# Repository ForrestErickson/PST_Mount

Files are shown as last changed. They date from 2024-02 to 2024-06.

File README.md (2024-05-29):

# Mount for Personal Solar Telescope
**WARNING NEVER LOOK AT THE SUN THROUGH A TELESCOPE, BINOCULARS, NAKED EYE, unless you have a known safe solar filter and you know how to use it.** 
Never make a home made filter out of unknown materials.  
Galileo was blind at the end of his life. I do not know how he observed sun spots, but he did. And he went blind. 

## Motivation
Several friends in the Smoky Mountain Astronomical Society, aka **[SMAS](https://groups.io/g/smokymtnastro)**, have the Coronado PST.  
I am hoping to help make them easier to use.  
I watched them try to use a camera tripod where the user has to loosen both the altitude and the azimuth axis by turning knobs, and then move the telescope in both axis to recenter the sun and then tighten both axis hoping that there is not stored spring energy (flex) in the tripod legs and then letting go only to have the sun poorly centered. Visitors at public events where the telescope owners wanted to share the experience were more often away from the eye piece than looking through it as the telescope owner was frequently repointing the telescope.
A tripod with a mass mounted to it forms something similar to a torsion pendulum and once disturbed it can take some time for oscillations do die down and novice observers bumping the telescope set them right back into motion.

The limited required altitude range of a solar telescope (only about 23 degrees above and below the celestial equator allows a small and sturdy table-top equatorial mount form factor which I set about to develop.

## CAD Drawing
Here is a photo made of the prototype part way through the development.


I want to not only build one or more mounts but share my work widely and so have placed my files and work on Github.
I used the free and open source 3D CAD modeling software FreeCAD to draw the parts and to combine them into an assembly to make the mount.

Of the first things I did was to model the Coronado Personal Solar Telescope starting with a sketch I found on the internet and with dimensions taken from a real telescope by one of the club members.
Made from measurements off a real PST 
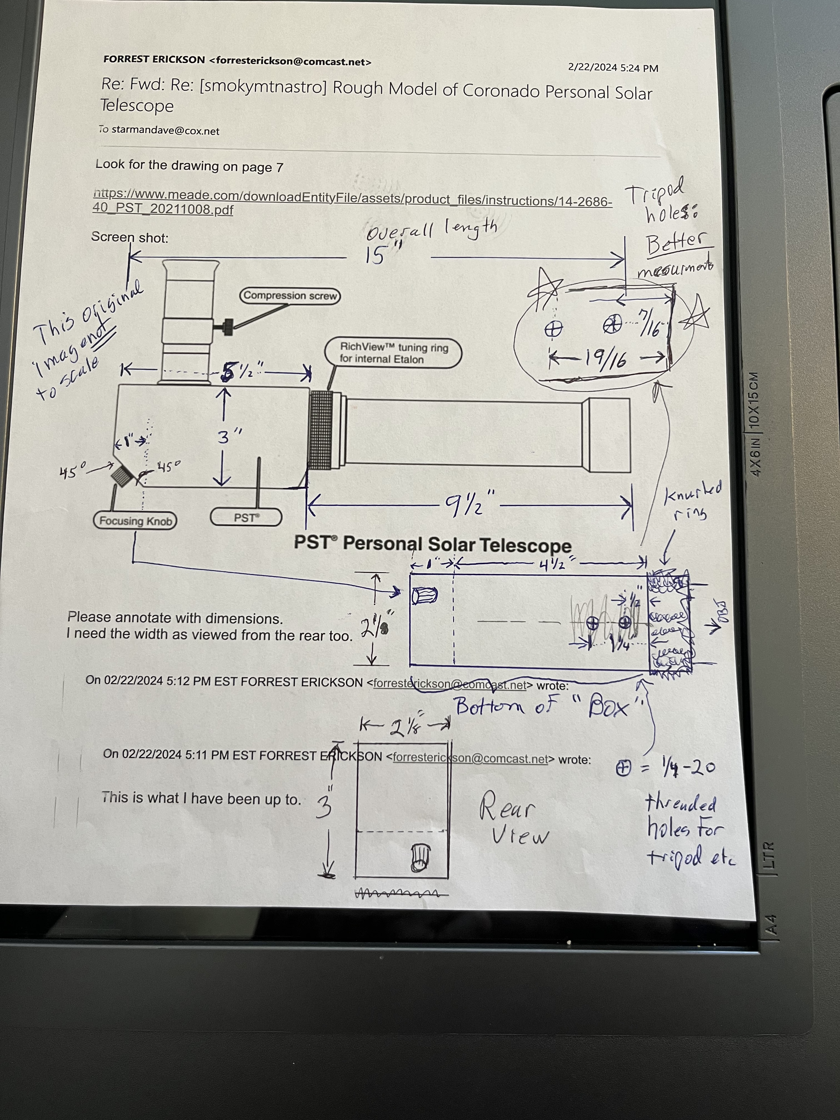
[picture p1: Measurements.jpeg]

From this drawing I made a 3D model of the body of the telescope (all but the long optical tube) and printed it out with an amusingly hollow body. TO this body I attached a cardboard tube approximating (but a bit smaller) than the real optical tube. 

## Prototype
An isometric view of  
<a
href="FabricationPhotos/WithWedgeIso.jpg">Image of: an isometric view.  
</a>

## Project Summary
* Drawn in FreeCAD and using A2Plus work bench.  
* Drawing for the PST (Personal Solar Telescope) is only from a side view photograph and will not be accurate.  A part was 3D printed to help with my trial and error fabrication and iterative design.  
* The size of the base is arbitrarily based on a 254 mm (10") disk (Hexagon) about 12.5 mm (1/2") thick.  Base set for latitude near Maryville TN of 35.5 Degrees.
* Right Assention Pin is 1/4" (About 25.4 /4 mm).
* Before the 20240408 solar eclipse I fabricated four of these and got three into the hands of PST users so that they might benifit during the eclipse.  

## License and Warranty
  **License**: This project and files are dedicated and released to the public domain.  
  **Warranty:** This project and files are designed to kill you and render the earth uninhabitable, however they not guaranteed to do so.

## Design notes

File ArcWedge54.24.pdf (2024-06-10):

Wedge 54.24 degrees.

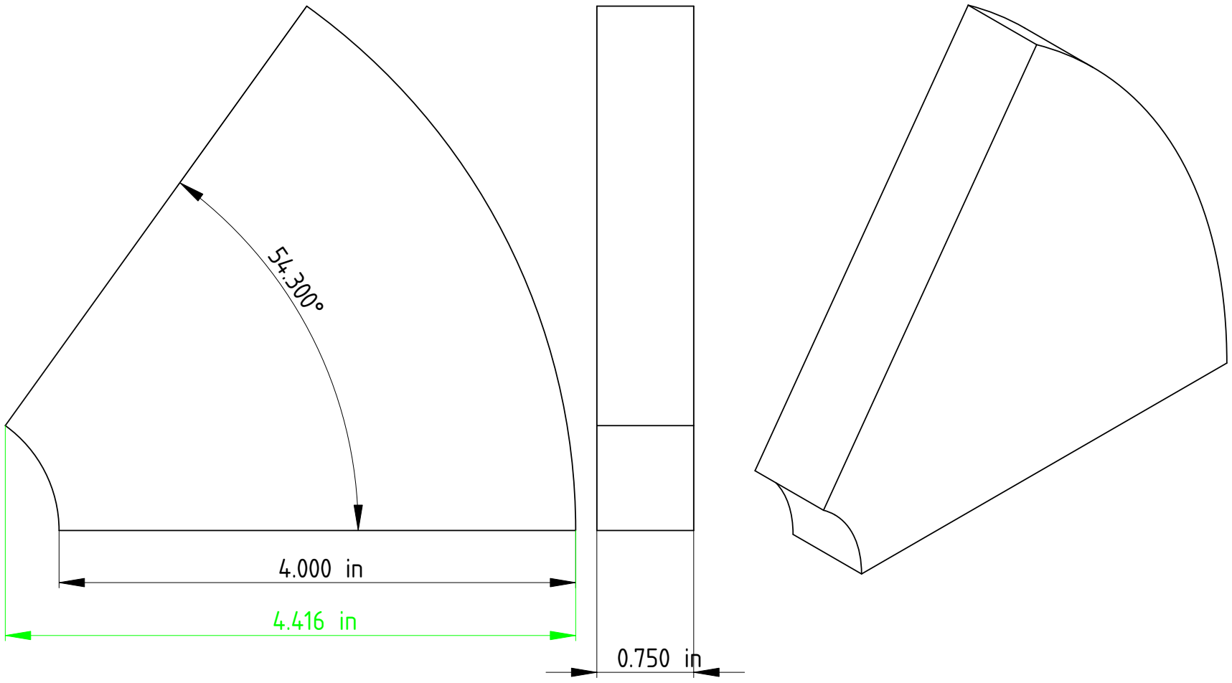
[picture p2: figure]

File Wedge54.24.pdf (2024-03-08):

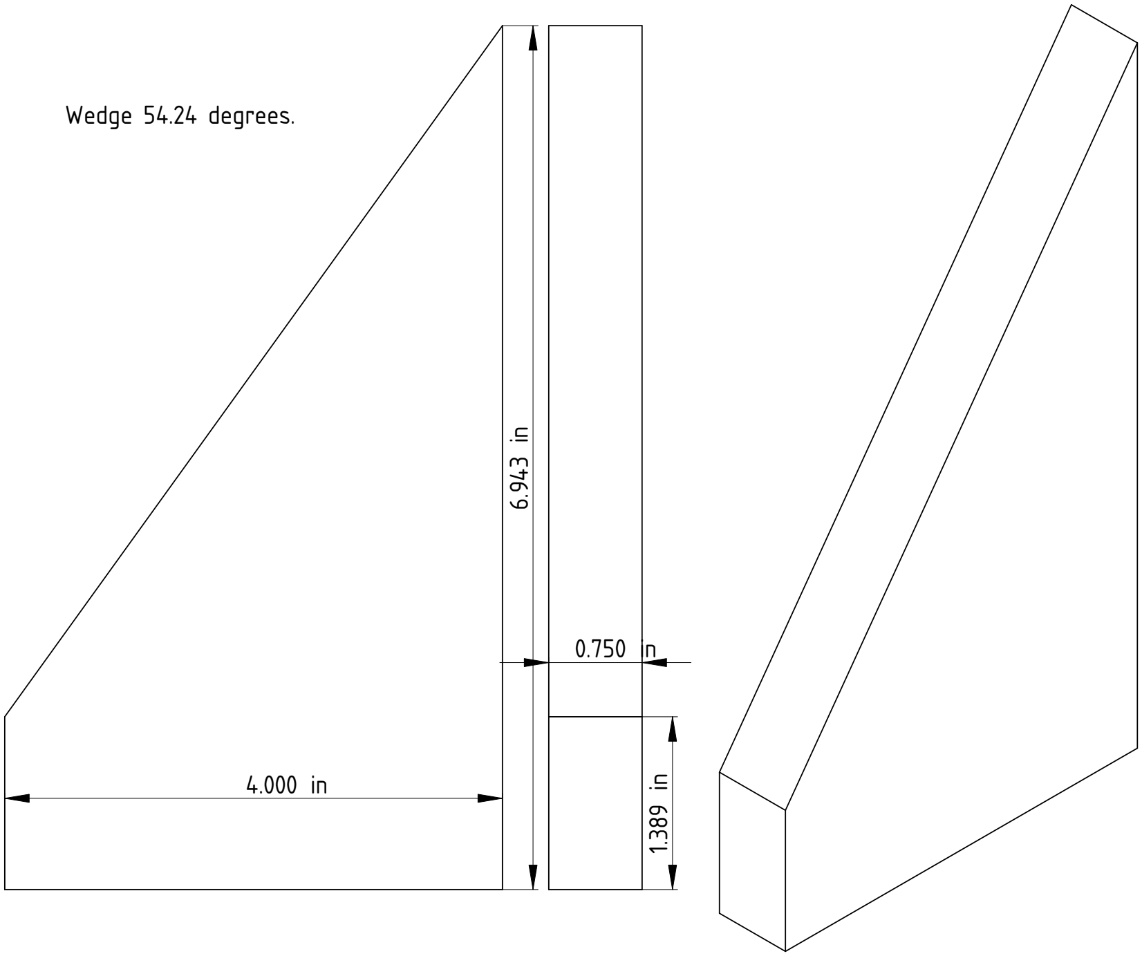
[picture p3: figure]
Wedge 54.24 degrees.

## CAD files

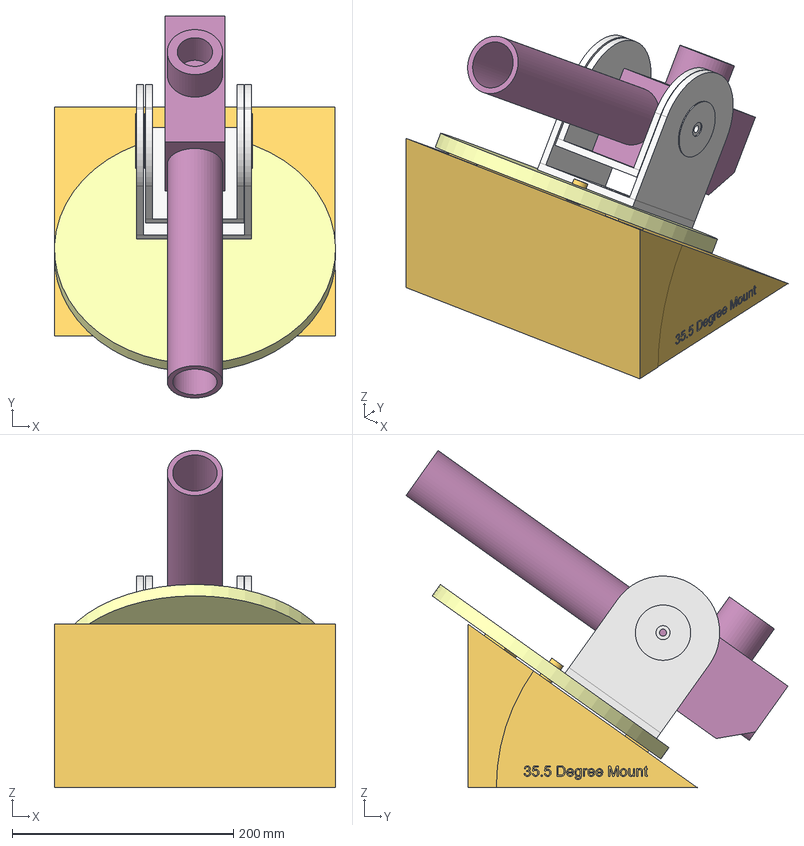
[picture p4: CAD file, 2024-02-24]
RAMountAssy_PST.FCStd
254.0 x 345.1 x 304.5 mm
Base35.5Degree_001
RAdisk_001
Pivot_Altitude_PST_001
Pivot_Fork_001
PST_Only_001

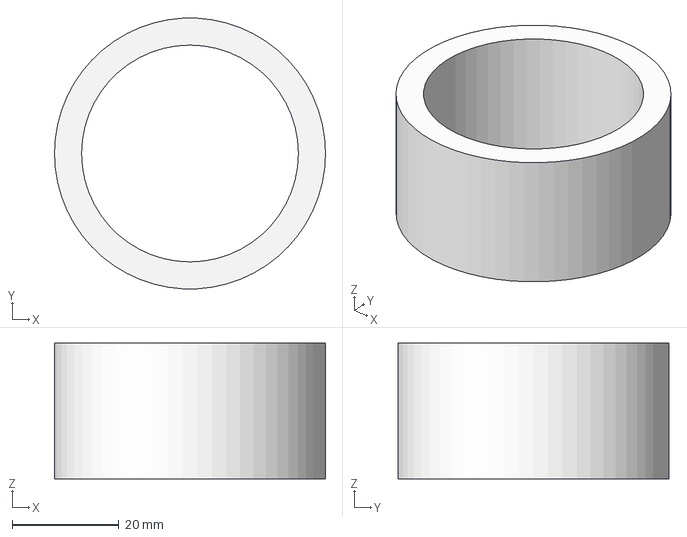
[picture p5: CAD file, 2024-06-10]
AdaptCardboardTube-Body.step
50.8 x 50.7 x 25.4 mm

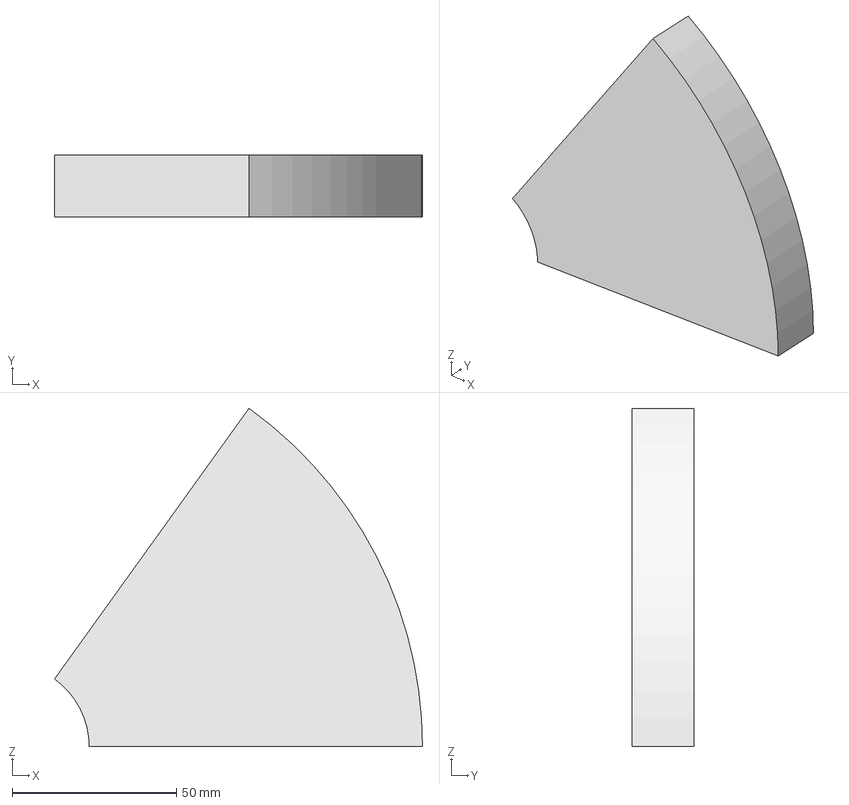
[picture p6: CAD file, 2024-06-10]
ArcWedge54.24Degrees.FCStd
112.2 x 19.1 x 103.1 mm

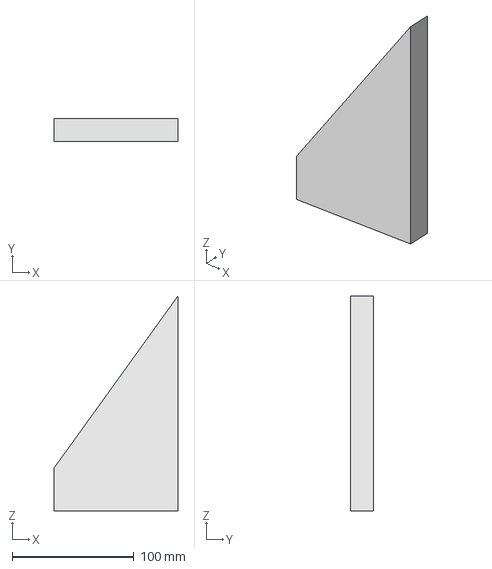
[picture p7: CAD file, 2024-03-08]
Wedge54.24Degrees.FCStd
101.6 x 19.1 x 176.3 mm

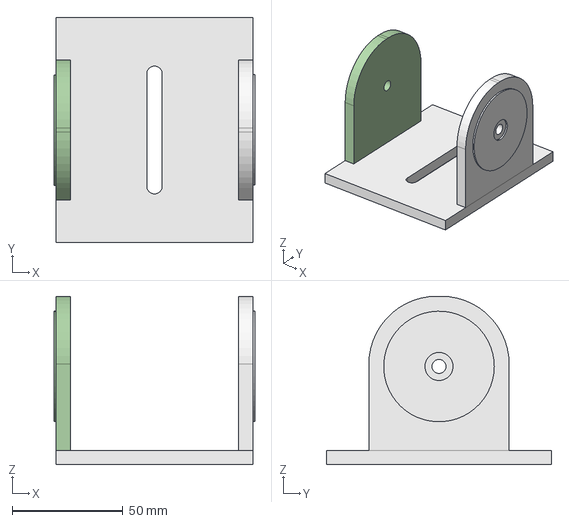
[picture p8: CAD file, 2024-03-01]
Pivot_Altitude_PST.FCStd
90.9 x 101.6 x 76.2 mm
BodyPivotLeft
BodyClonePivotRigh

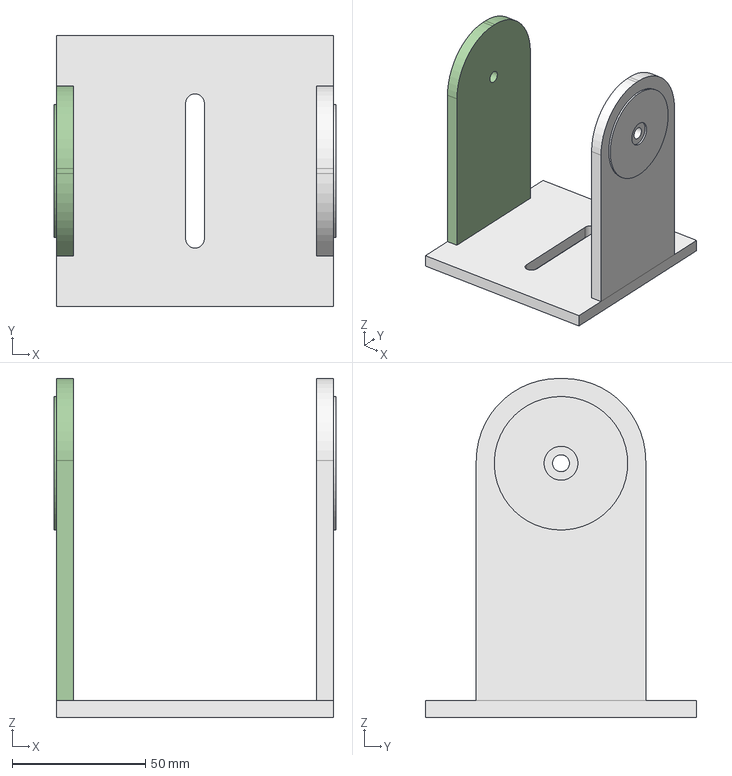
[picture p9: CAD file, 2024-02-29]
Pivot_Fork.FCStd
105.6 x 101.6 x 127.0 mm
BodyForkLeft
BodyCloneRighFork

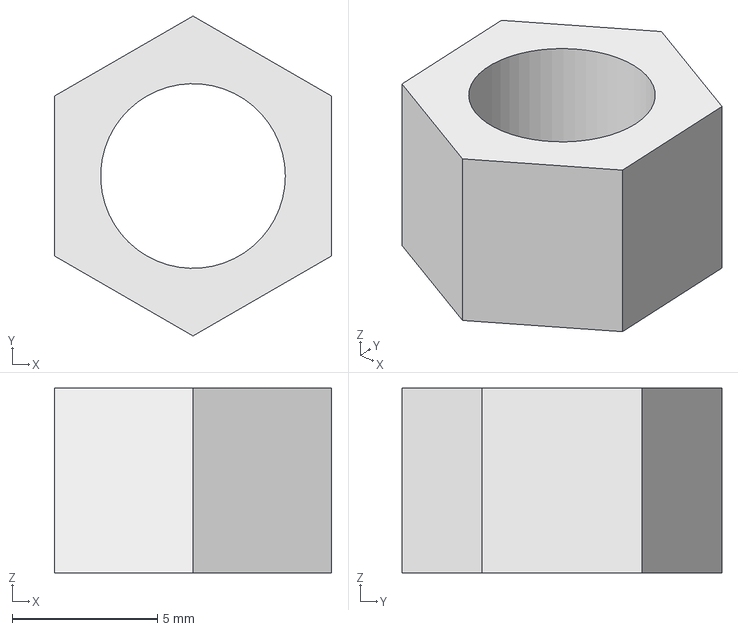
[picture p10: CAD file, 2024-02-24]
NutHex0.25-20.FCStd
9.52 x 11.0 x 6.35 mm

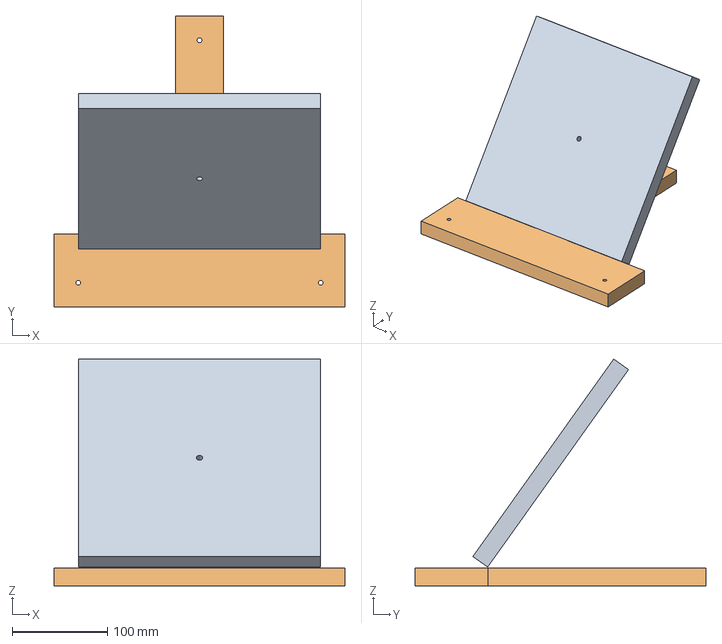
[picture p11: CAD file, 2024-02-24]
PST_BaseAdj.FCStd
304.8 x 304.8 x 237.6 mm
BodyPlatform
BodyFeet

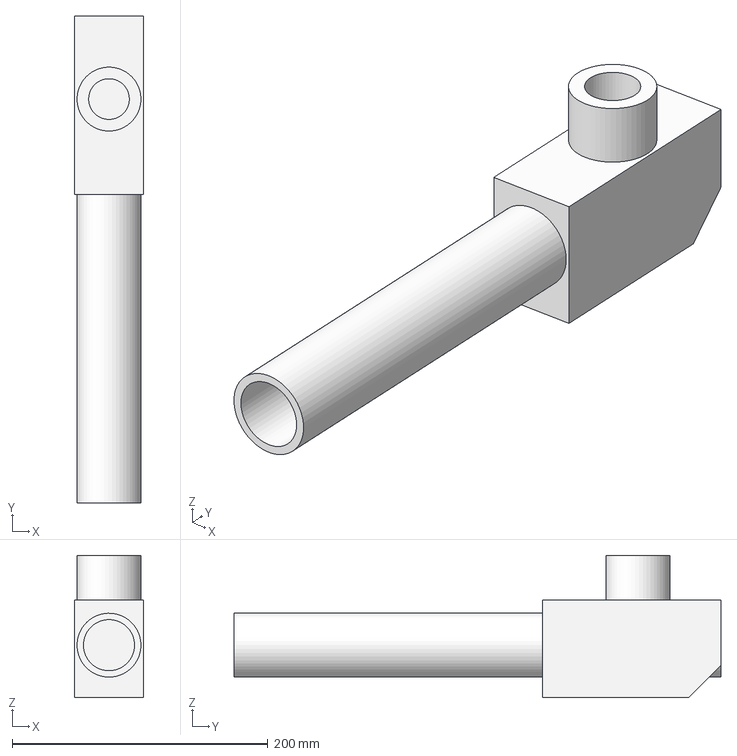
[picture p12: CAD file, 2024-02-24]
PST_Only-EntirePST.step
54.0 x 381.0 x 111.2 mm

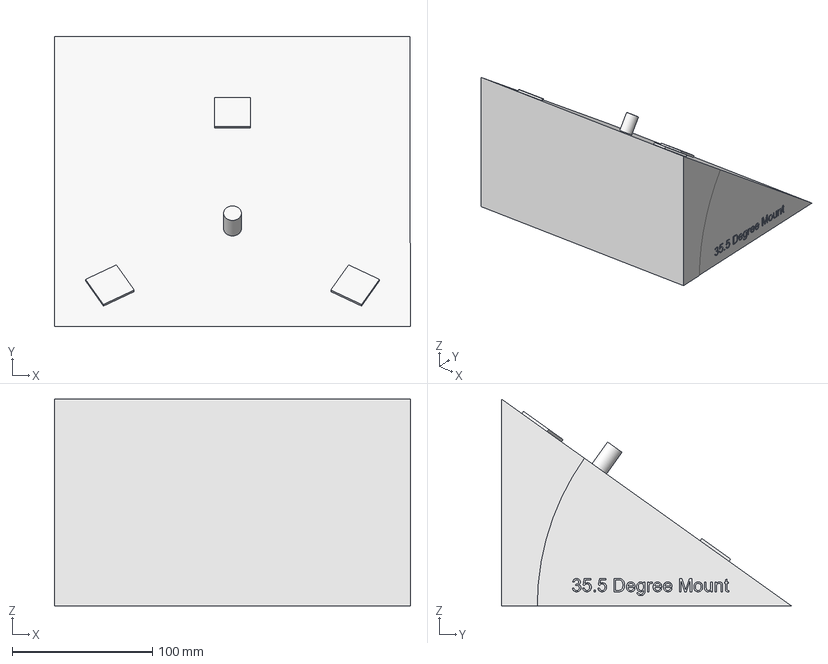
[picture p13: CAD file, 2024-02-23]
Base35.5Degree.FCStd
254.0 x 206.8 x 147.5 mm

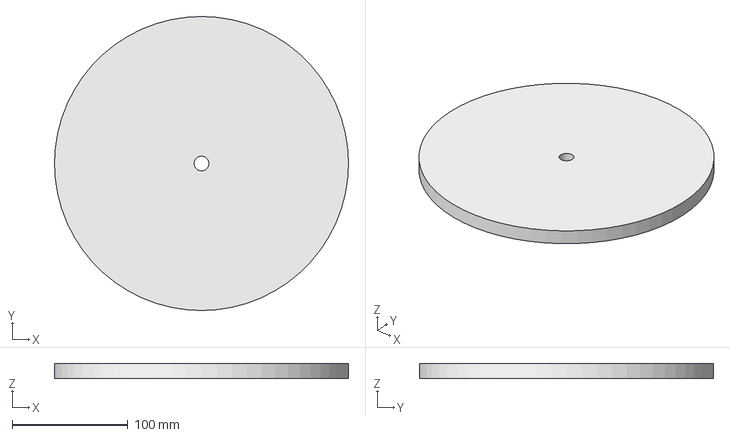
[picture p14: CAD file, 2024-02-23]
RAdisk.FCStd
254.0 x 254.0 x 12.7 mm

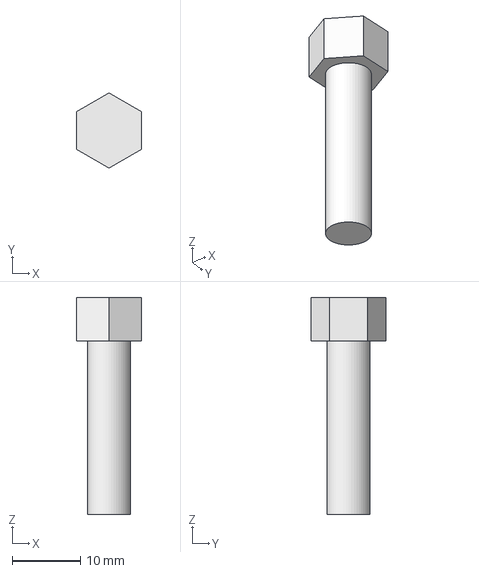
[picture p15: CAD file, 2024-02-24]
Bolt_Hex_0.25x1.FCStd
9.53 x 11.0 x 31.8 mm

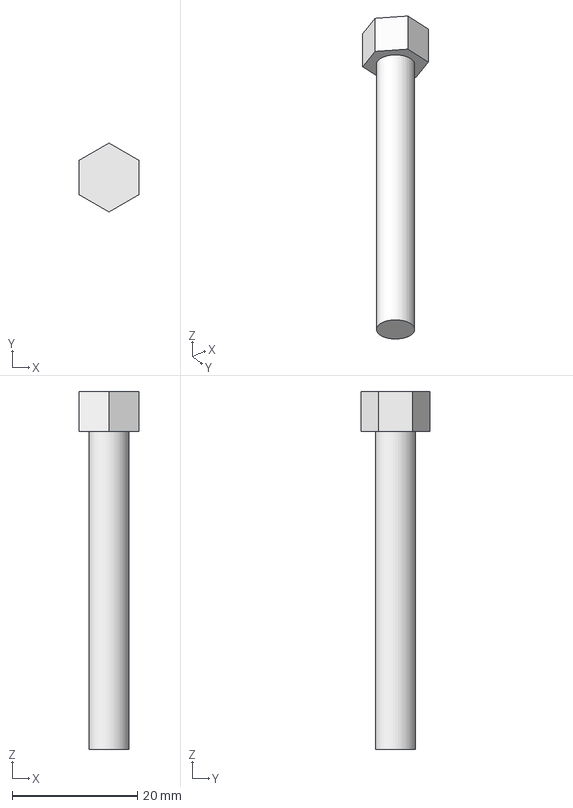
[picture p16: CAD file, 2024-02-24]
Bolt_Hex_0.25x2.FCStd
9.53 x 11.0 x 57.1 mm

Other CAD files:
AdaptCardboardTube.FCStd
PST_Only.FCStd

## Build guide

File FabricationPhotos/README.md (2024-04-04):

# Fabrication Photos
Personal Solar Telescope Mount.  
Hoping to get one finished for our next club meeting on 8 March 2024.   
***Reflections:  ***
My welding looks better under the slag.  I am way out of practice.  
I am suspecting that I need a heaver rod. I am using 5/64" rod type E6013.  Welder is set for 55 amps. The steel is 1/8" and so at the "T" joints I am welding 1/4" of material.  

## Paper Templates to guide fabrication.  
Apply painters tape and then the Paper Templates glued are glued to the tape. Removes much easier that way   
<a
href="PaperTemplates.jpg">Image of: Apply painters tape and then the Paper Templates glued are glued to the tape. Removes much easier that way.  
</a>
  
## Drilling Pilot Holes  
First 1/8 inch at high speed, 2700 RMP.   Then 1/4 inch at 1700 RPM.  
<a
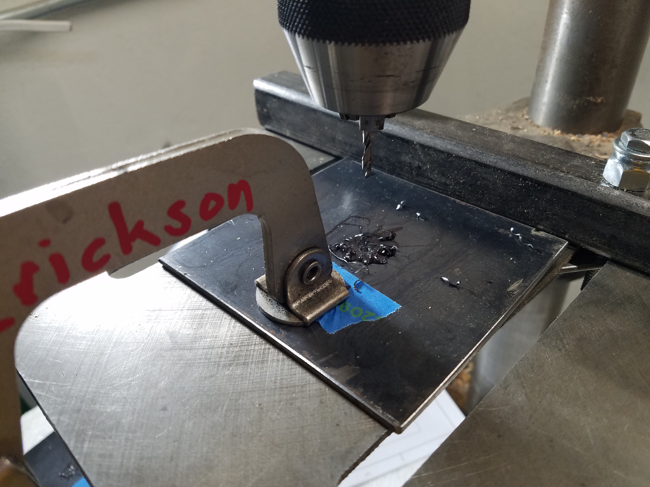
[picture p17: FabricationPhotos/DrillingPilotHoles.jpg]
Image of: Drilling Pilot Holes on drill press.
href="DrillingPilotHoles.jpg">  
</a>

## Grind Radius  
I first removed most of the material with the hand held angle grinder and cutoff wheel. Finished creeping up to the line with a belt sander at 80 grit then 120 grit. Wish I had 240 grit belts.  
<a
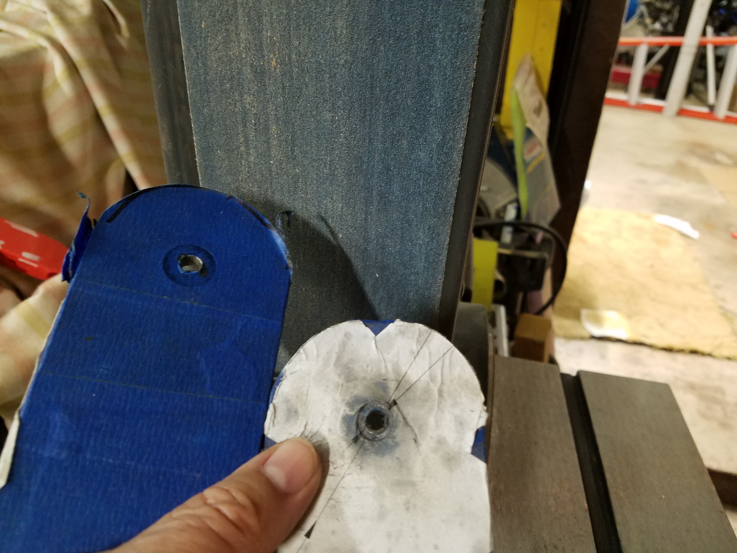
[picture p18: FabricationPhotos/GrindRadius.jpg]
Image of: Grind Radius with belt sander.
href="GrindRadius.jpg">  
</a>

## Welding Setup  
Holding the brackets in line and of the correct width with all thread 1/4-20" rod.  
The 90 degree magnets help a lot.  
<a
href="WeldingSetup.jpg">Image of: Welding Setup.  
</a>

## Making Welds  
Making the welds and using painters tape to reduce welding splatter. It was better than nothing but there was burn through and still splatter. Unfortunatly the glue stuck to the work and was difficult to clean off. I am trying oven cleaner just now.  
My welds look much better under the slag.  
The 90 degree magnets help a lot.  
<a
href="MakingWelds.jpg">Image of: Making Welds.  
</a>

## Stop Turing Alt Bolt
A stop to prevent turning of the altitude lock bold.  
<a
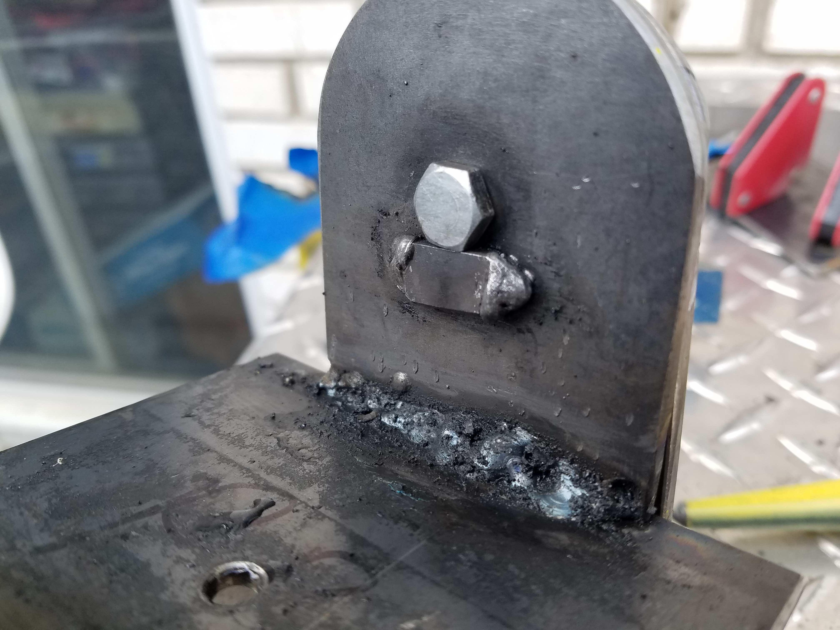
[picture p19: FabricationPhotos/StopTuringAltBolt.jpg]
Image of: Stop Turing Alt Bolt.
href="StopTuringAltBolt.jpg">  
</a>

## In the Paint Booth
Prime and paint  
<a
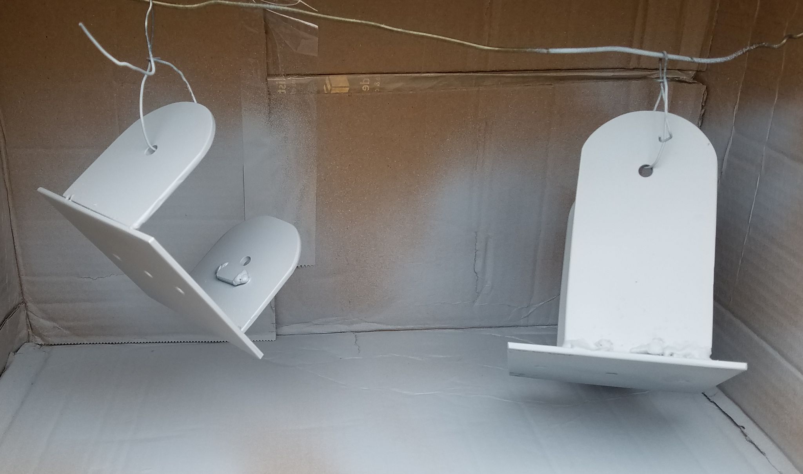
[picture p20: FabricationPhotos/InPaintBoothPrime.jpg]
Image of: Priming the the booth.
href="InPaintBoothPrime.jpg">  
</a>

With Silver Paint  
<a
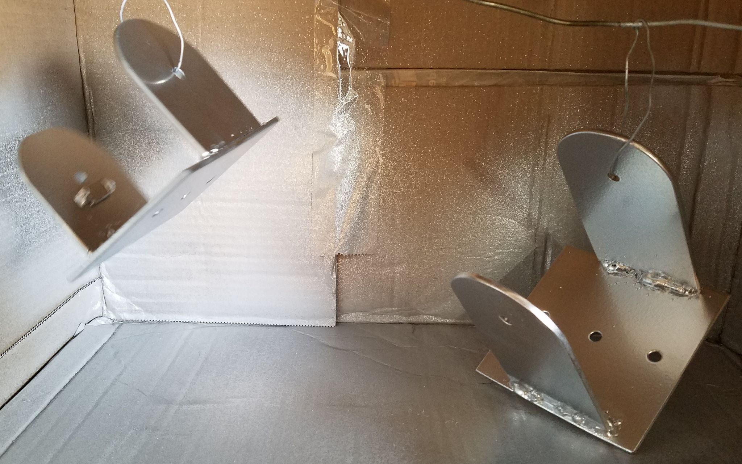
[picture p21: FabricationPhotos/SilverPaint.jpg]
Image of: brackets in sliver paint.
href="SilverPaint.jpg">  
</a>

## The Wood Working 
Improvising, the APE* parts.   

Rough Wood Work Side View  
<a
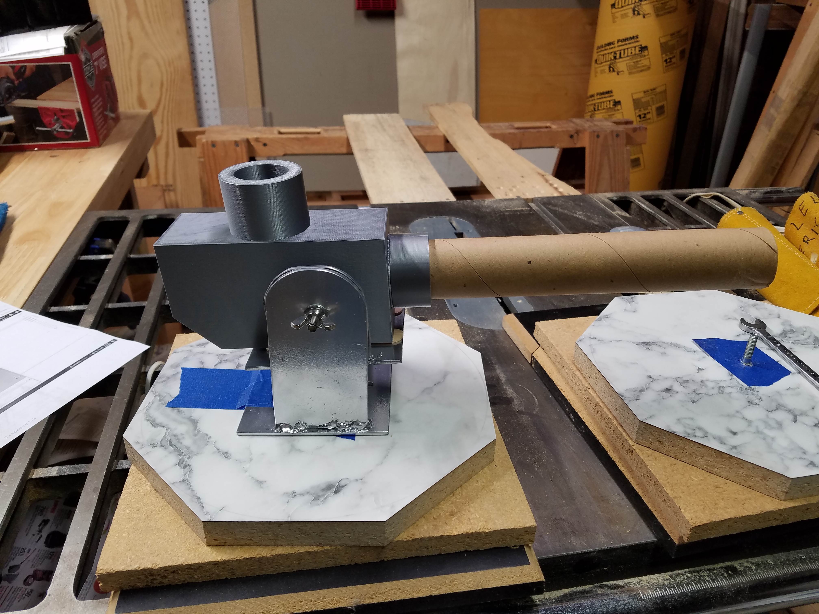
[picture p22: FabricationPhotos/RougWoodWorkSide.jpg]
Image of: It is starting to look like the goal.
href="RougWoodWorkSide.jpg">  
</a>
(* Available Parts Engineering)

Going to need to design a latitude block soon  
<a
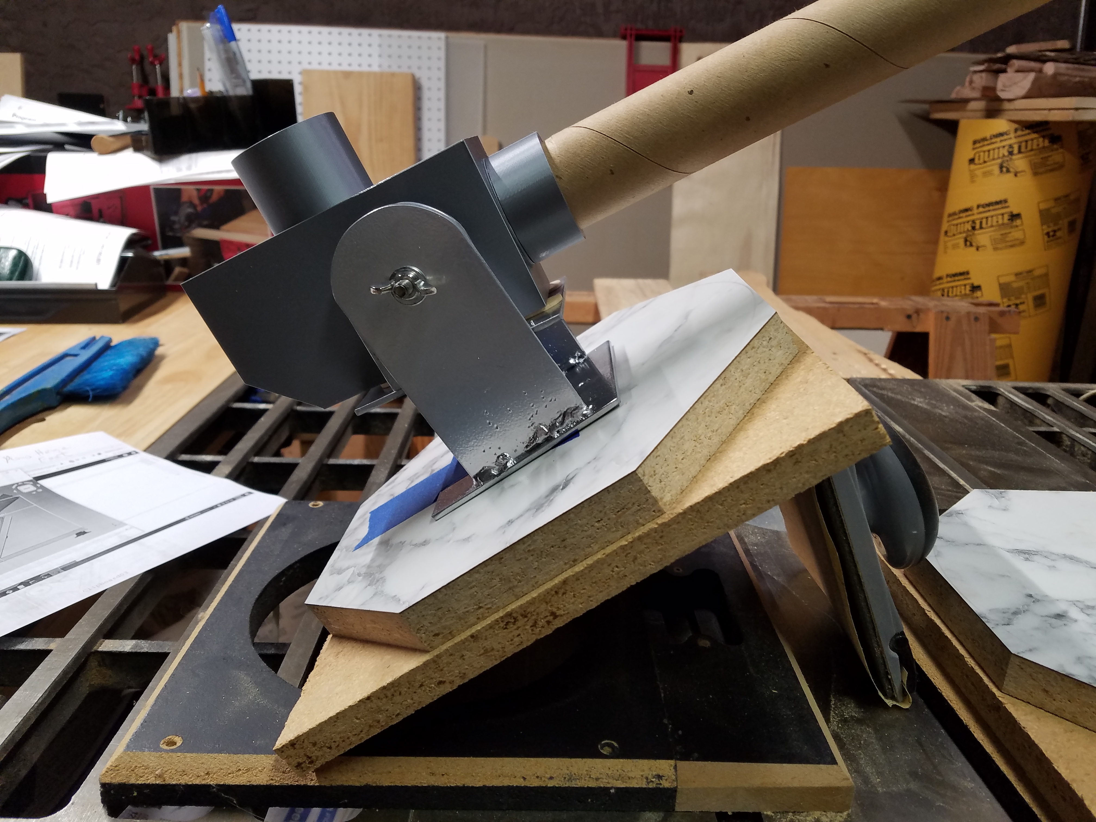
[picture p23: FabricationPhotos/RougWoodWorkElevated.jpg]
Image of: Side view with temporary eleviation block.
href="RougWoodWorkElevated.jpg">  
</a>  
Side view with temporary elevation block.

## Final Assembly
It is taking shape.  The skies will never clear.

An isometric view  
<a
href="WithWedgeIso.jpg">Image of: an isometric view.  
</a>

A side view  
<a
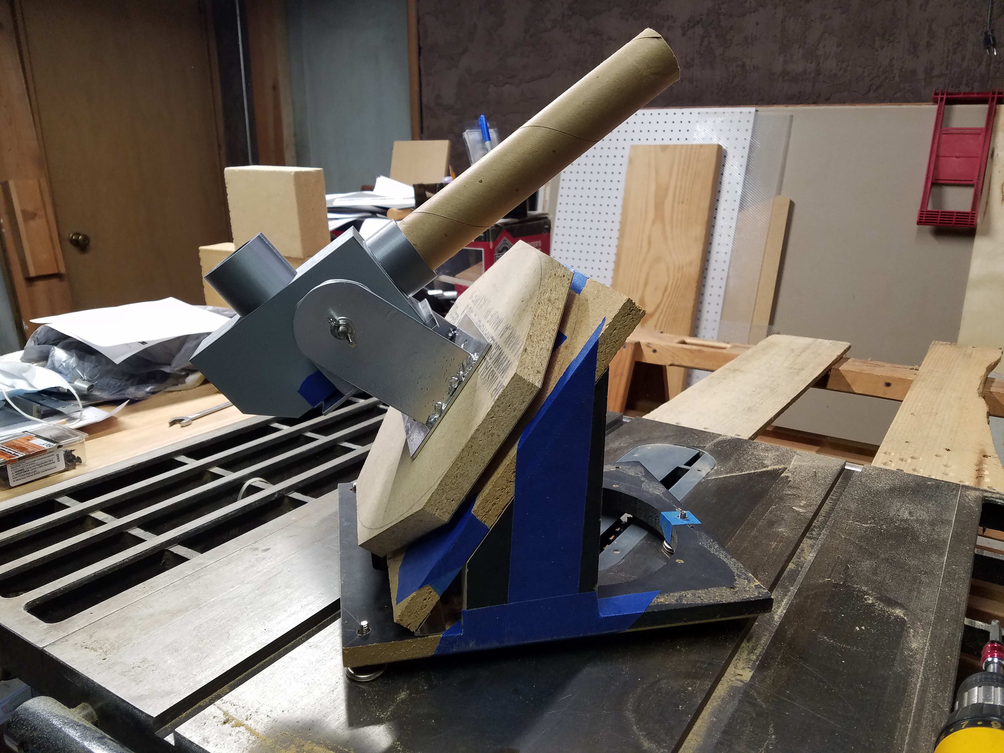
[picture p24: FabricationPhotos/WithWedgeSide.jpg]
Image of: side view.
href="WithWedgeSide.jpg">  
</a>

Similar with paint  


An innovation this morning (20240403).  
Retention feature for telescope mounting screw.  
Cut from a Landry detergent bottle.
Note this retention requires the rubber feet be thicker than the retention washer. 
  
I drilled one size under 1/4" and made four cuts.

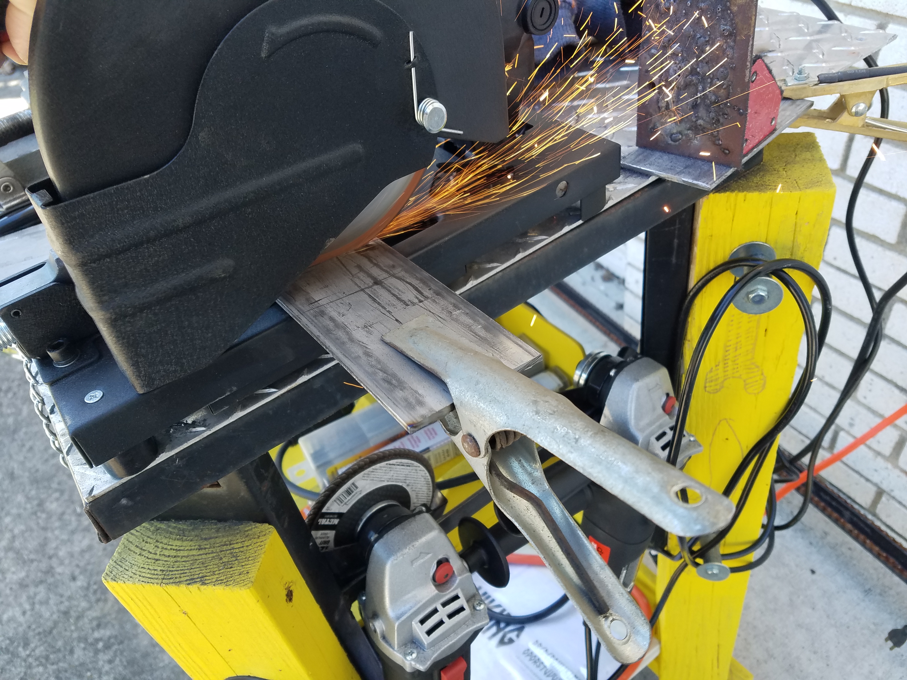
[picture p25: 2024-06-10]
FabricationPhotos/20240329_120654.jpg

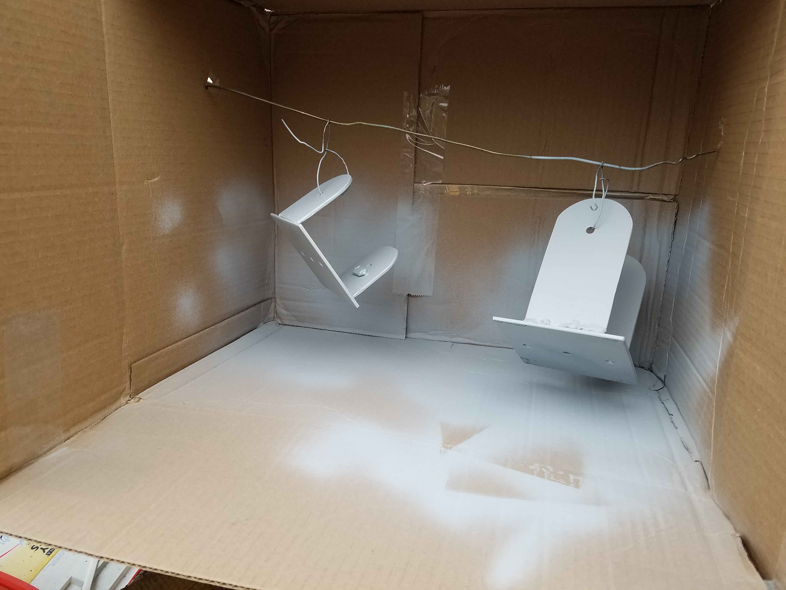
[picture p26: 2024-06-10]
FabricationPhotos/20240305_144243.jpg

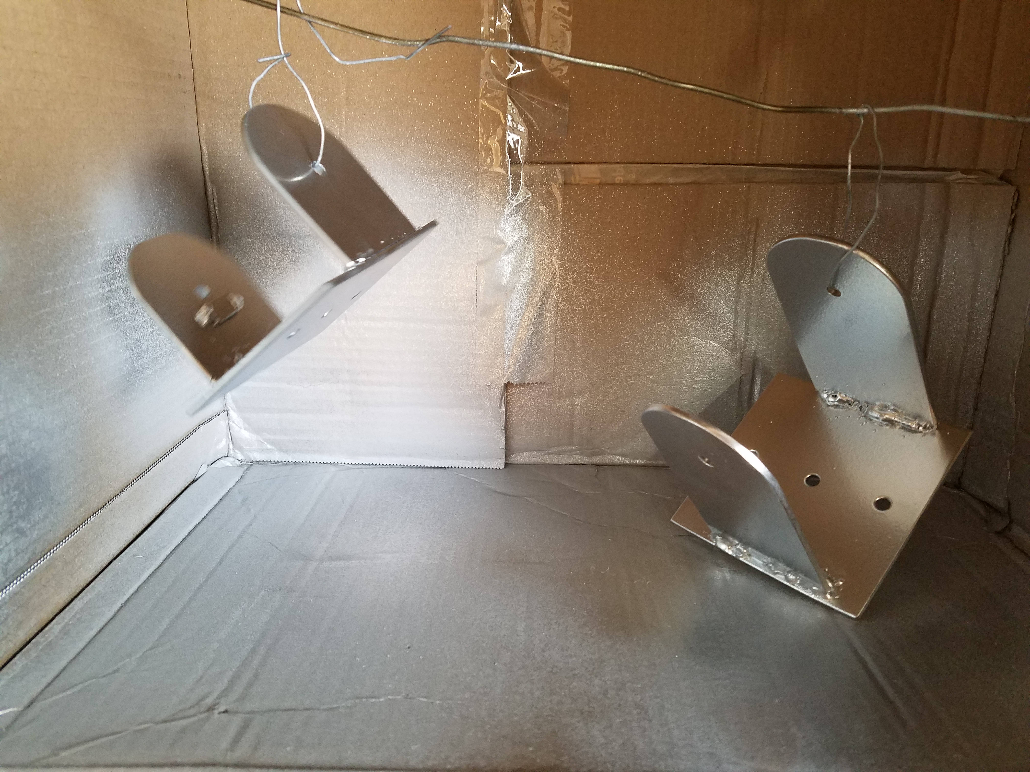
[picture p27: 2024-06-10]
FabricationPhotos/20240305_161416.jpg

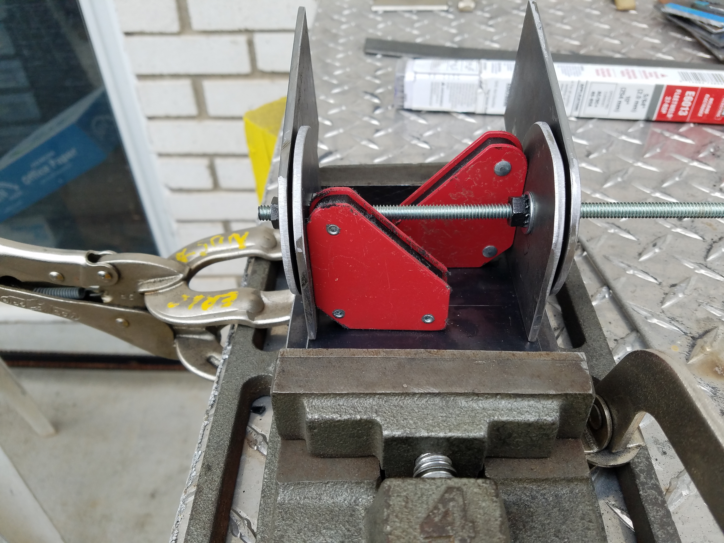
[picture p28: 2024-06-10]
FabricationPhotos/20240305_104548.jpg

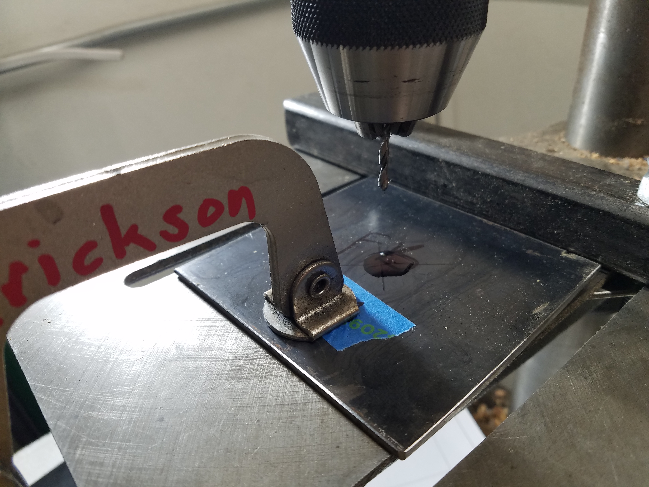
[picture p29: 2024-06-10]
FabricationPhotos/20240304_194700.jpg

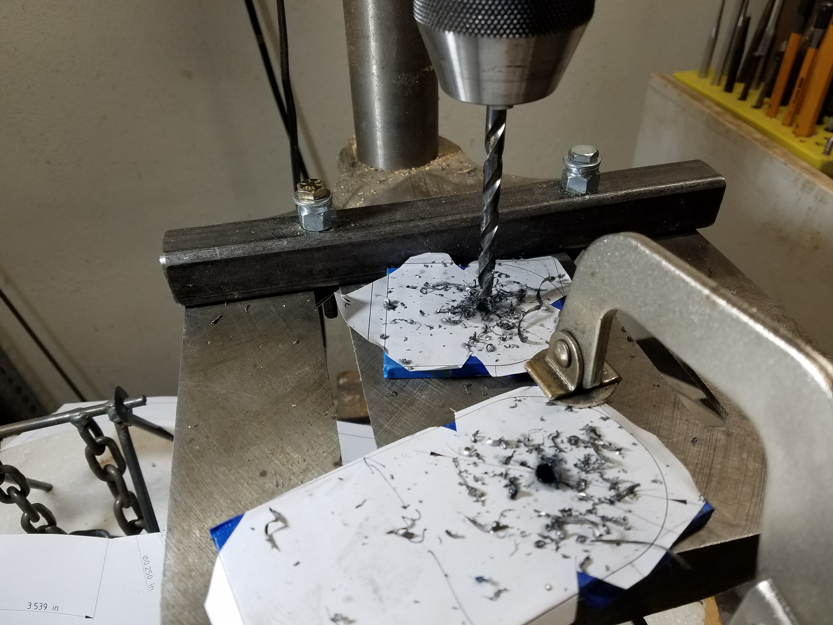
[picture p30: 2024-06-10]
FabricationPhotos/20240304_195852.jpg

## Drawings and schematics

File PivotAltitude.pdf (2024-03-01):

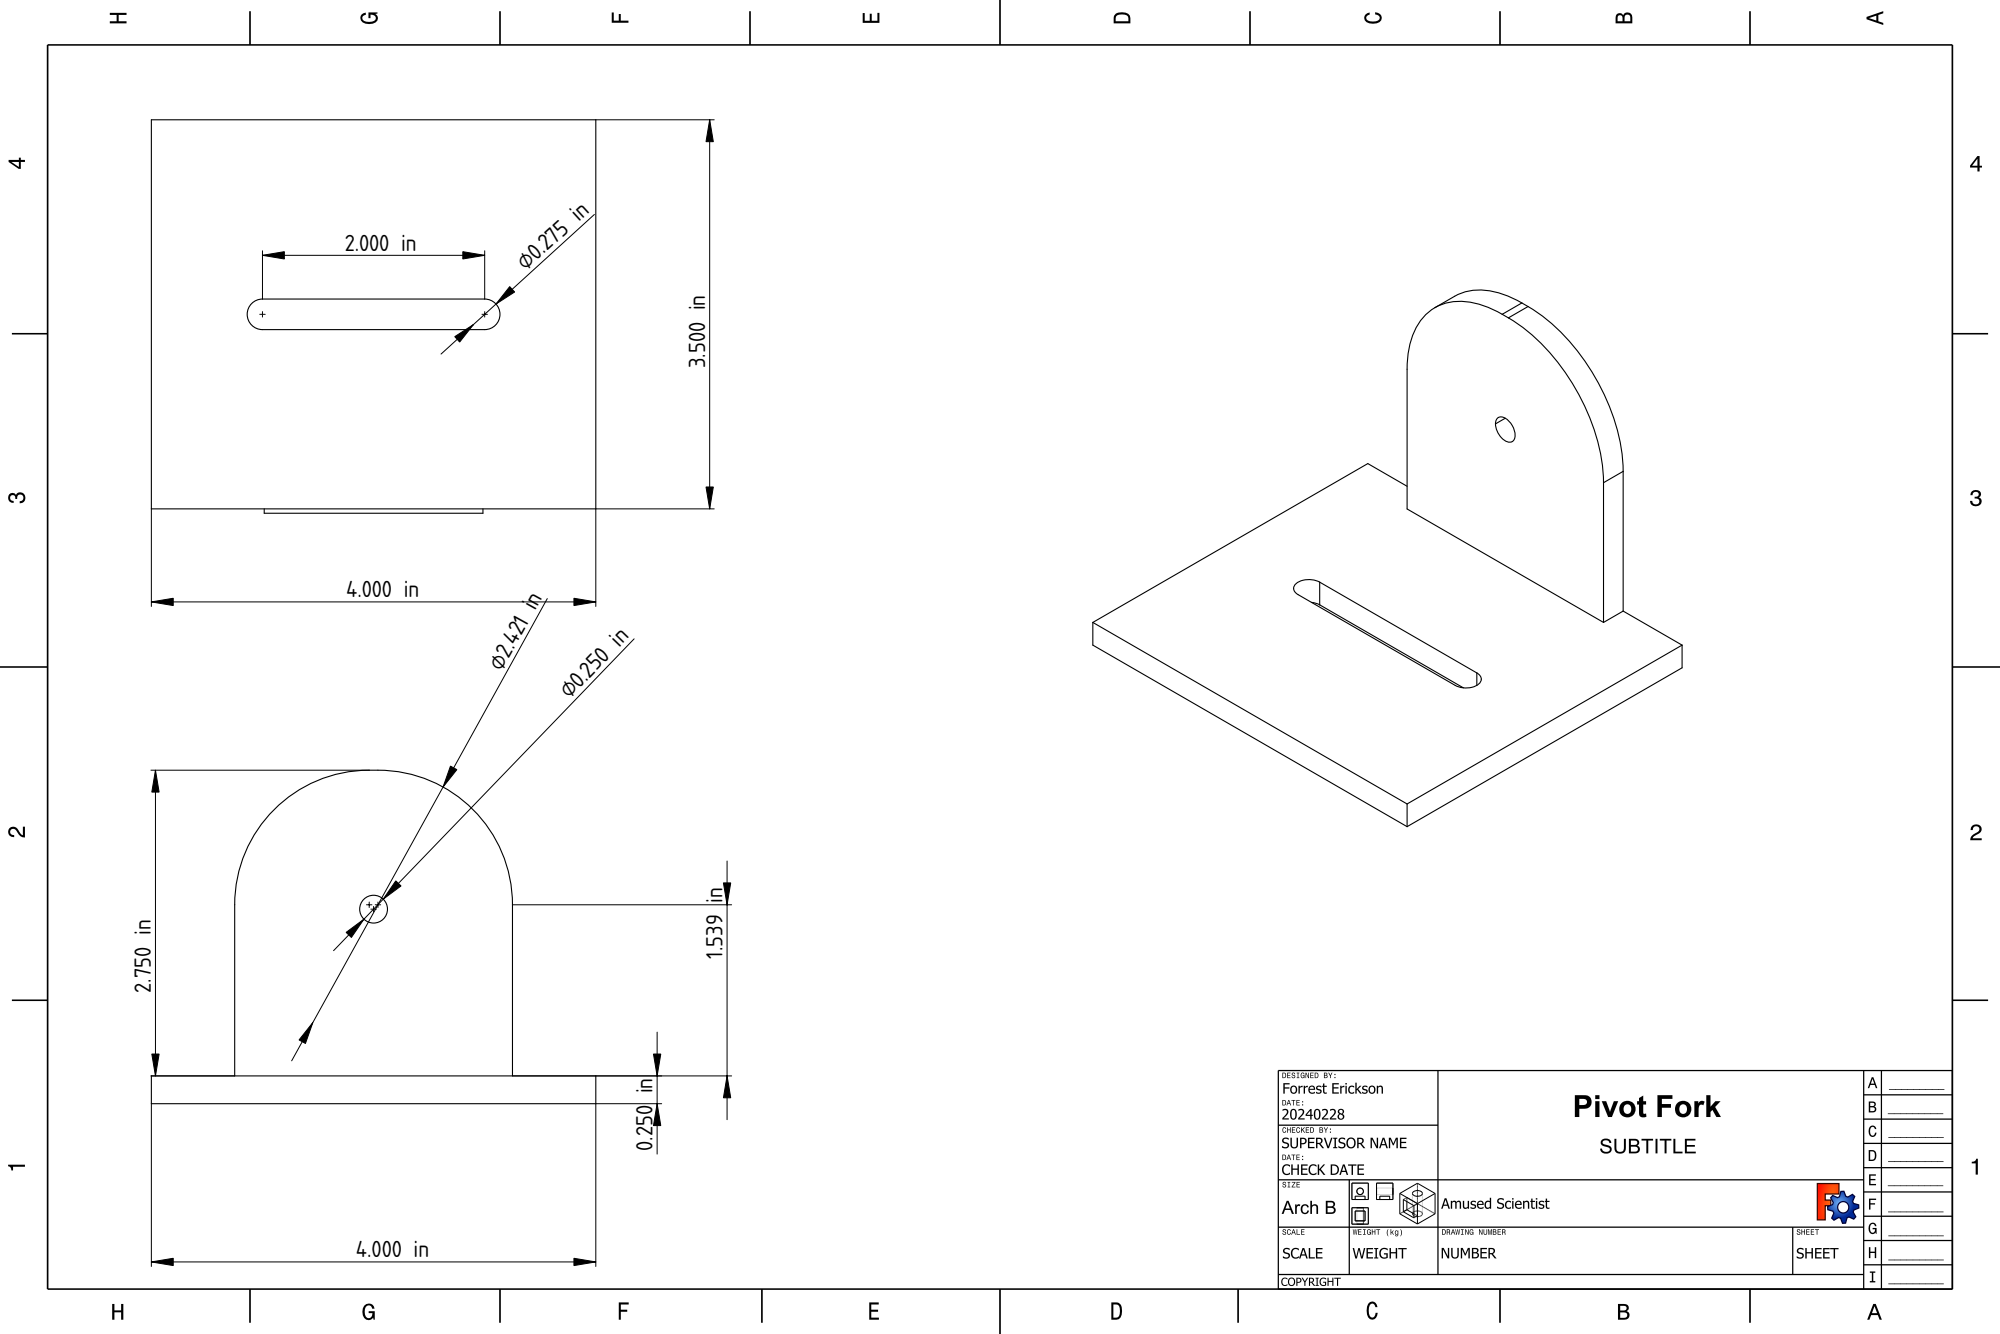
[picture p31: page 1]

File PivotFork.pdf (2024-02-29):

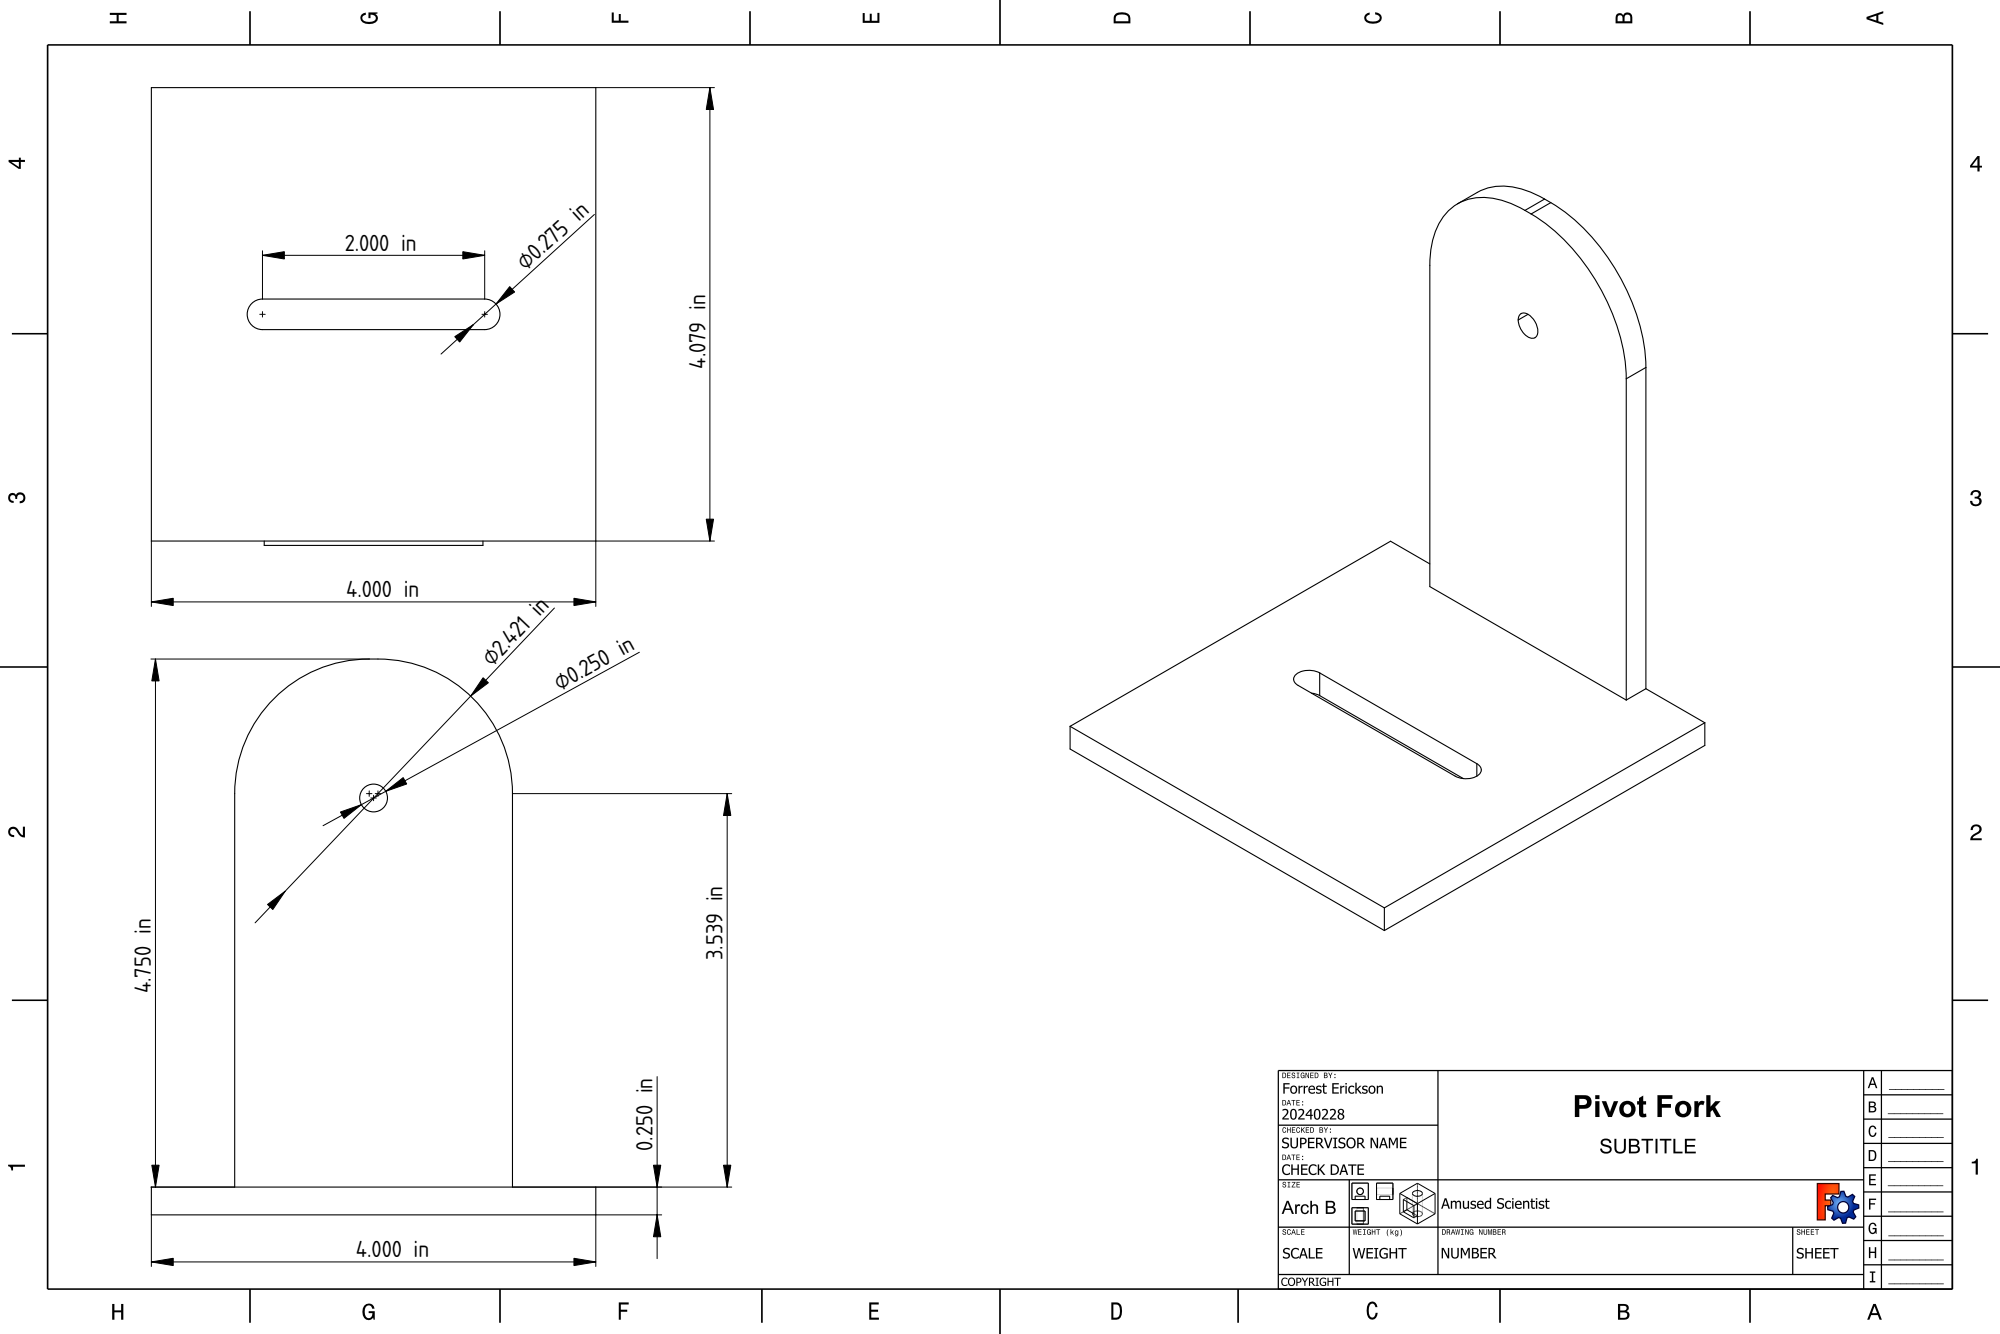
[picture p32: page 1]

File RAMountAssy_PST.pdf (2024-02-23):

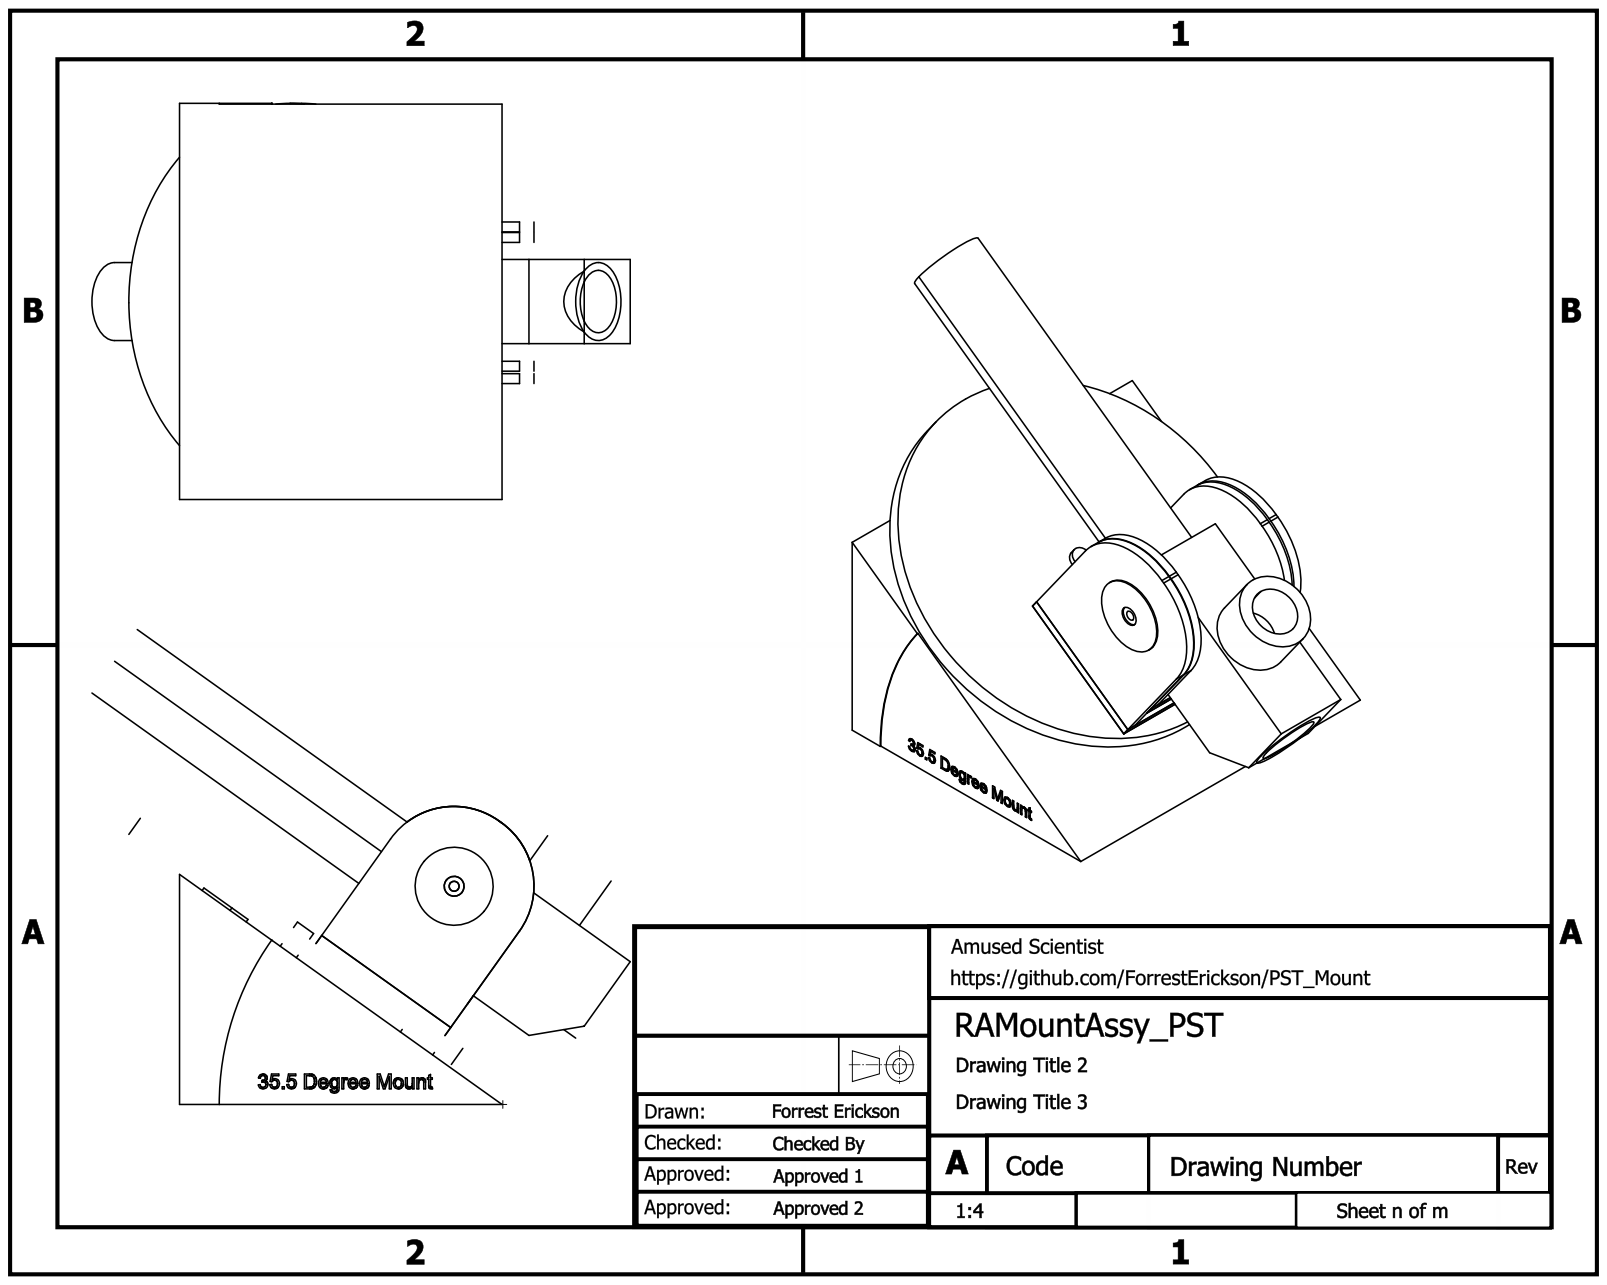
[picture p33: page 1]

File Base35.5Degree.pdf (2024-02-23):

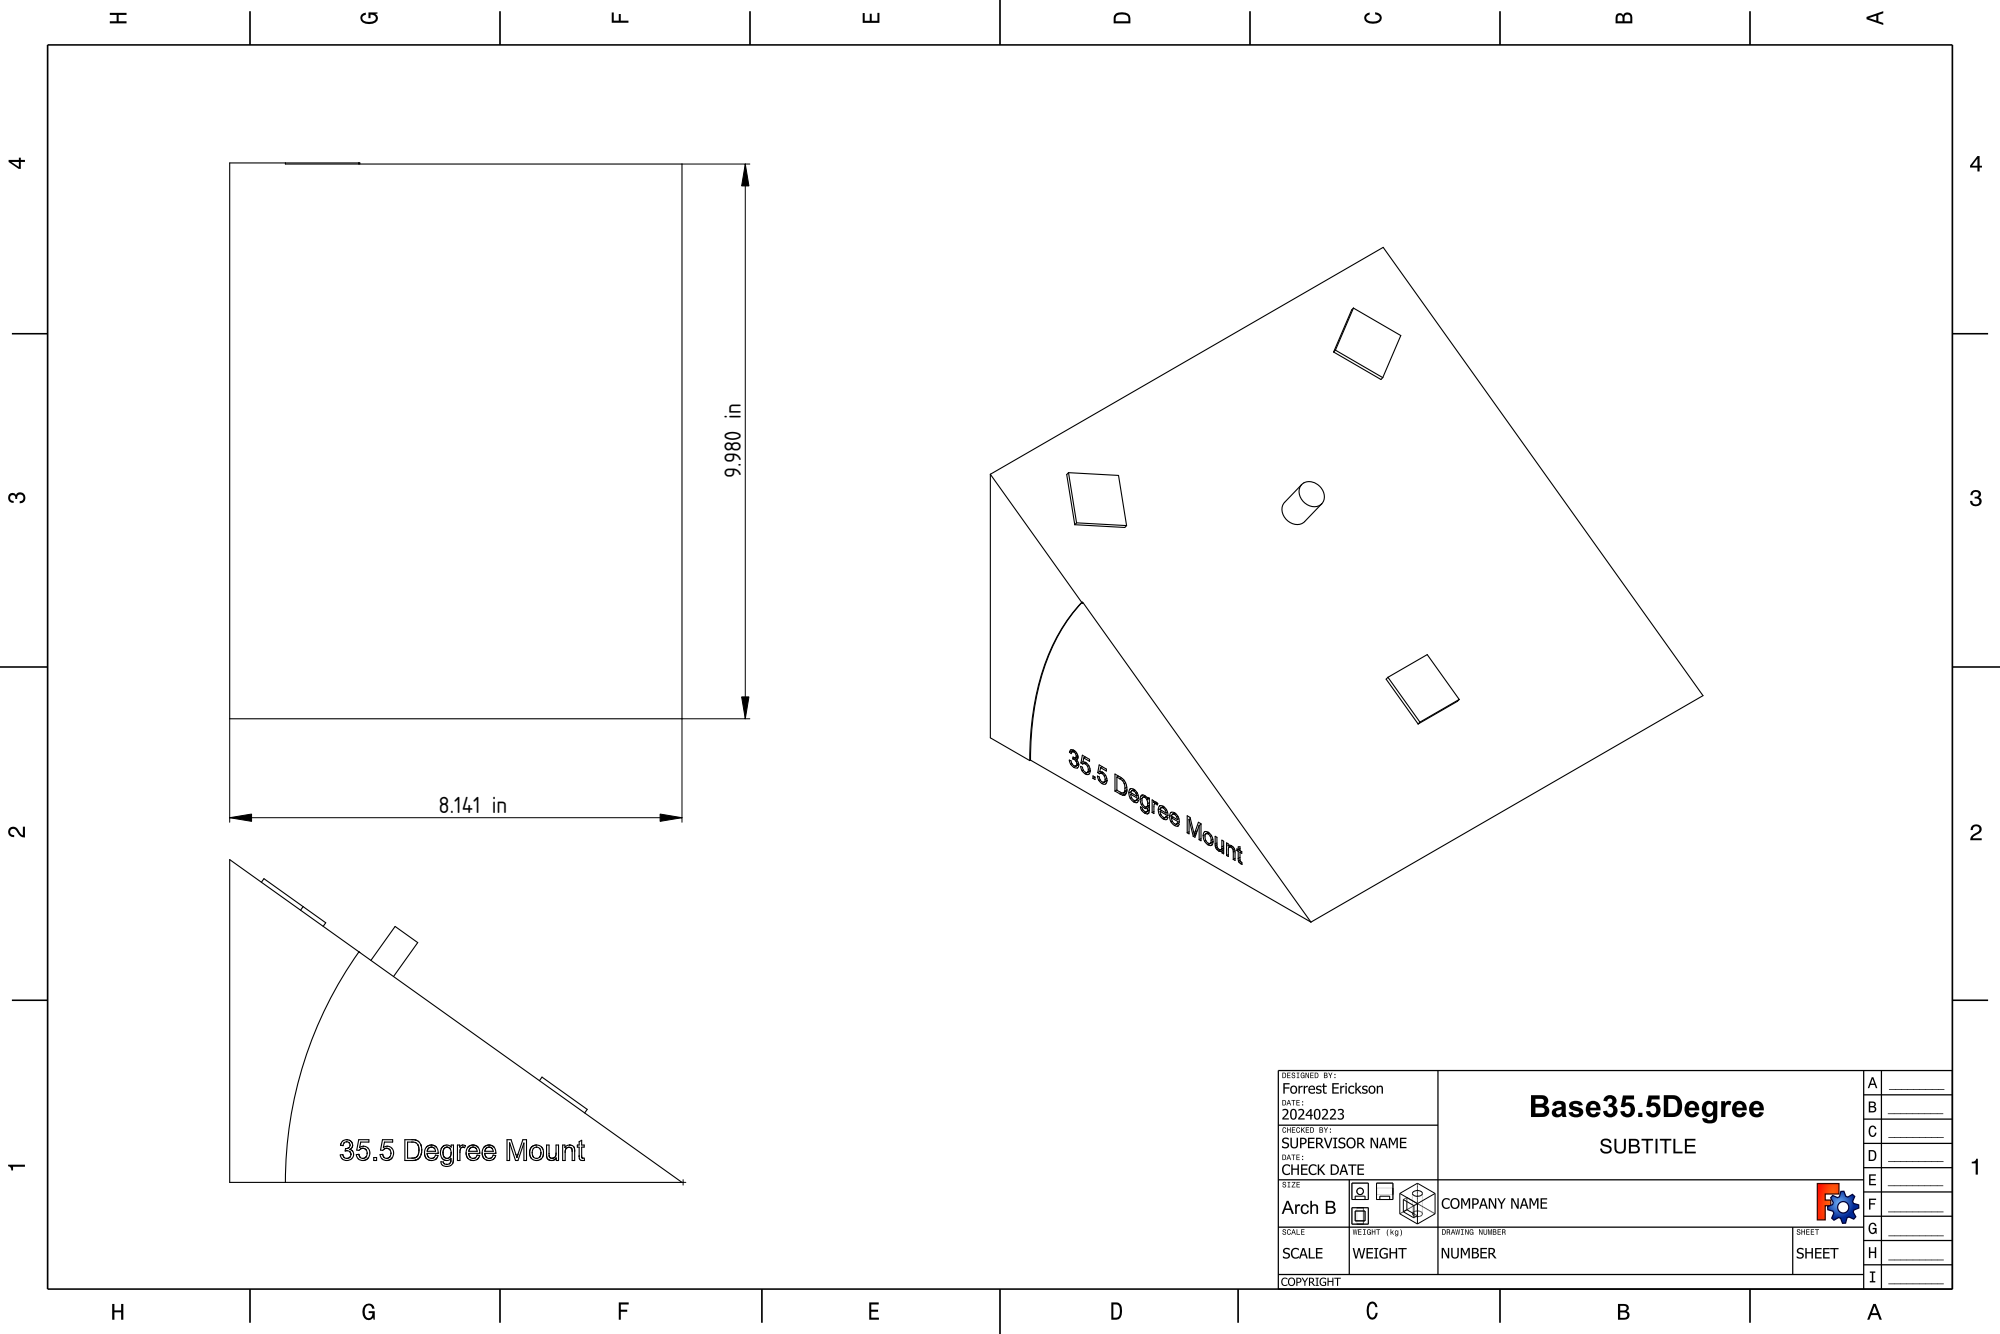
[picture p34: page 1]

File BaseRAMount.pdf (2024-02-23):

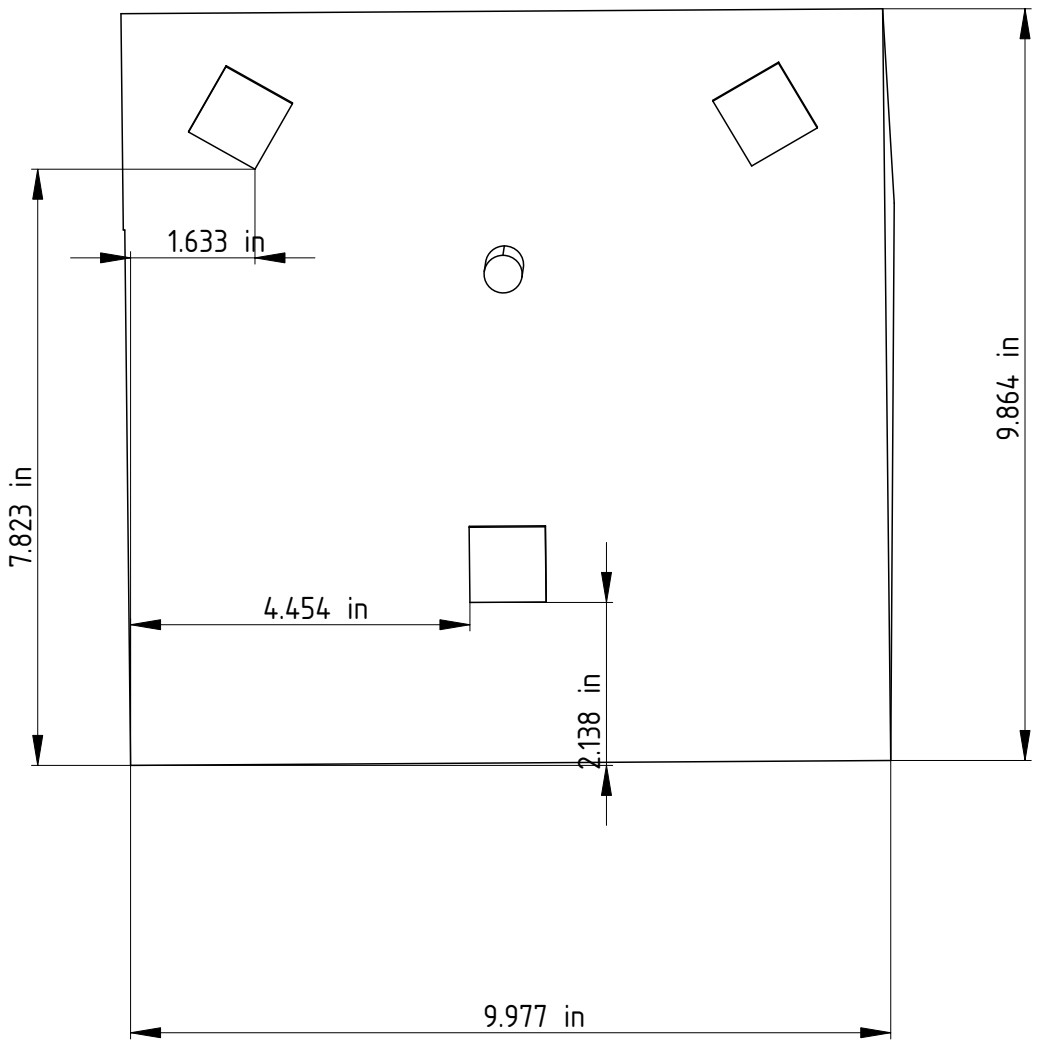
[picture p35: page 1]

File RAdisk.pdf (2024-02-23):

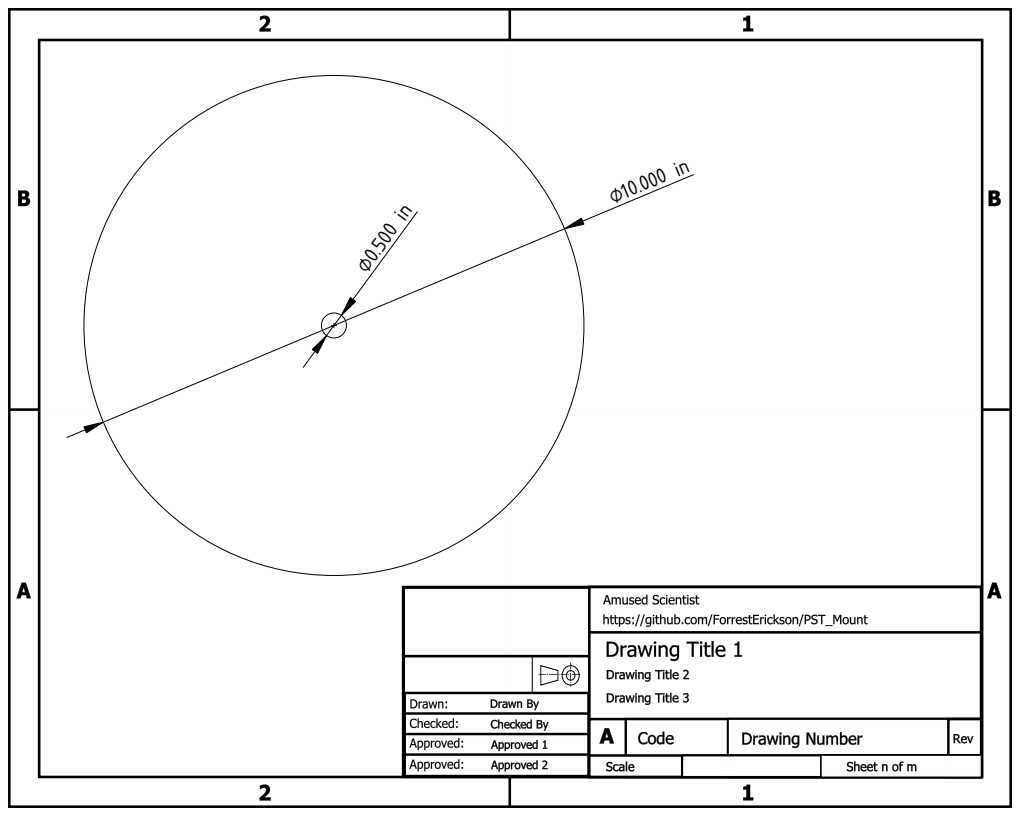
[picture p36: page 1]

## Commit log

2024-02-22 Initial commit. PST, Base, RAdisk.
    [Base35.5Degree.FCStd, PST_Only.FCStd, RAMountAssy_PST.FCStd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]
2024-02-22 Add a pivot part.
    [Pivot_Altitude_PST.FCStd, RAMountAssy_PST.FCStd]
2024-02-22 Add a fork drawing. Add to assembly.
    [Pivot_Altitude_PST.FCStd, Pivot_Fork.FCStd, RAMountAssy_PST.FCStd]
2024-02-23 Add image of Mount Assy. Update base with text, Add bevel and focus knob to OTA. Update assy with the above.
    [Base35.5Degree.FCStd, PST_Only.FCStd, RAMountAssy_PST.FCStd]
2024-02-23 Update with measurements from an actual PST.
    [PST_Only.FCStd, Pivot_Altitude_PST.FCStd, Pivot_Fork.FCStd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]
2024-02-23 Add some PDF files for fabrication.
    [Base35.5Degree.FCStd, PST_Only.FCStd, Pivot_Altitude_PST.FCStd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]
2024-02-23 Add PDF for mount.
    [RAMountAssy_PST.FCStd]
2024-02-23 Add PDF for mount assy.
2024-02-24 Add a new base.
    [PST_BaseAdj.FCStd, RAMountAssy_PST.FCStd]
2024-02-24 Add and adjustable base design. Step file for PST too.
    [Bolt_Hex_0.25x1.FCStd, Bolt_Hex_0.25x2.FCStd, PST_Only-EntirePST.step]
2024-02-24 Add fork, altitude and PST with bolts.
2024-02-24 Base and assembly updated.
    [PST_BaseAdj.FCStd]
2024-02-24 Add hex nut
    [NutHex0.25-20.FCStd]
2024-02-25 Update README.md
    Update screen shot of telescope on mount.
2024-02-25 Add length to fork. Remove length from altitude.
    [Pivot_Altitude_PST.FCStd, Pivot_Fork.FCStd]
2024-02-26 Resise the width of the fork vertical left and right.
    [Pivot_Fork.FCStd]
2024-02-27 Pull new narrow fork into assembly. SetApperance colors for parts.
2024-02-29 Update PDF drawing of fork with new dimensions.
    [Pivot_Fork.FCStd]
2024-03-01 Make pivot out of modified fork.
    [Pivot_Altitude_PST.FCStd]
2024-03-01 Rename internal to the pivot.
    [Pivot_Altitude_PST.FCStd]
2024-03-01 Update assembly with new pivot. Lots of contraints removed.
2024-03-01 Update assembly with new contraints.
2024-03-01 Update PDF of PivotAltitude.
    [Pivot_Altitude_PST.FCStd]
2024-03-06 Add photos of painting fork and altiude bracket.
2024-03-08 Add new drawing for a wedge. Add wedge to assembly. Update fabrication readme.
    [AdaptCardboardTube.FCStd, Wedge54.24Degrees.FCStd]
2024-04-04 Update README.md
    Add photo of prototype including the 3D printed telescope place holder.
2024-04-04 Update README.md
    Add photo of prototype after painting.
    Added photo of retaining feature for the telescope mounting screw.
2024-05-29 Update README.md
    Add detail to the motivation story of the mount.
2024-05-29 Add more to the assembly.
2024-06-10 Make a latatude wedge with arcs. Add to assembly drawing.
    [ArcWedge54.24Degrees.FCStd]
2024-06-10 Add an adapter to allow gluing a card board tube to the telesope body.
    [AdaptCardboardTube-Body.step]
